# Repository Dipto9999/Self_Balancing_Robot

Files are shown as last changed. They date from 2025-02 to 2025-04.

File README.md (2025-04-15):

# WALL-E (Self Balancing Robot)

## Contents

* [Overview](#overview)
  * [Features](#features)
  * [Components](#components)
* [System Design](#system-design)
  * [Functional Diagram](#functional-diagram)
  * [Architecture Diagram](#architecture-diagram)
* [Robot Firmware](#robot-firmware)
  * [Arduino](#arduino)
  * [STM32](#stm32)
* [User Software](#user-software)
  * [Driver App](#driver-app)
  * [Dashboard App](#dashboard-app)
* [Demonstration](#demonstration)
* [Credit](#credit)

---

## Overview

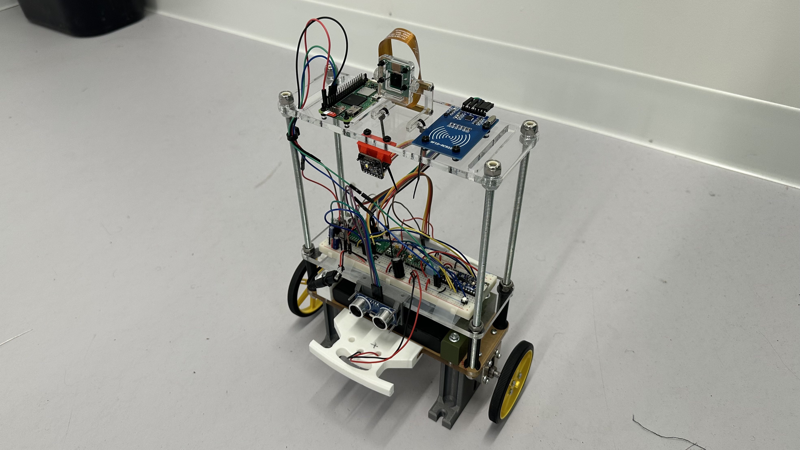
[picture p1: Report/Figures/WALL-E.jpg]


We designed **WALL-E**, an autonomously balancing two-wheel robot driven wirelessly via Bluetooth.

### Features

WALL-E prioritizes safe navigation and secure access.

- Detects the nearby environment (i.e. obstacles, color recognition)
- Prevents unauthorized control with **RFID** authentication and BLE pairing code.
- Generates live camera feed and uploads to **AWS S3** cloud storage.

### Components

- **Microcontrollers**:
  - Arduino Nano 33 BLE Sense Rev2 (Balancing & BLE)
  - STM32L051K8T6 (Environmental Sensors, Auth)
  - Raspberry Pi Zero 2 W (Camera Feed)

- **Sensors and Modules**:
  - BMM150 IMU
  - HC-SR04 Ultrasonic Distance Sensor
  - TCS34725 Color Sensor
  - RC522 RFID Module
  - CEM-1302 Buzzer
  - Freenove 5MP Camera

- **Actuation**:
  - DRV8833 Motor Drivers
  - Pololu 37D DC Motors

---

## System Design

### Functional Diagram

<p align="center">
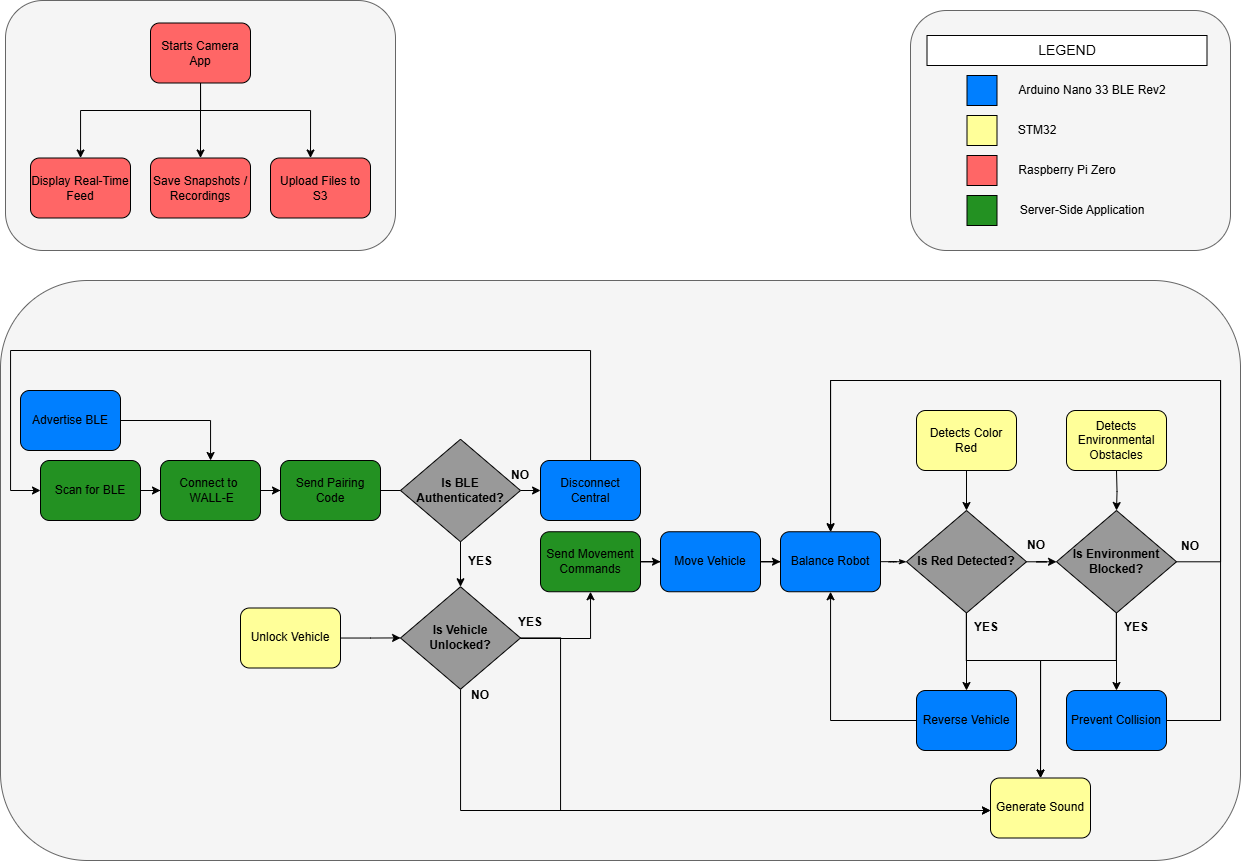
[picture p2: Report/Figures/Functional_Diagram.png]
Functional Diagram
  
</p>

### Architecture Diagram

<p align="center">
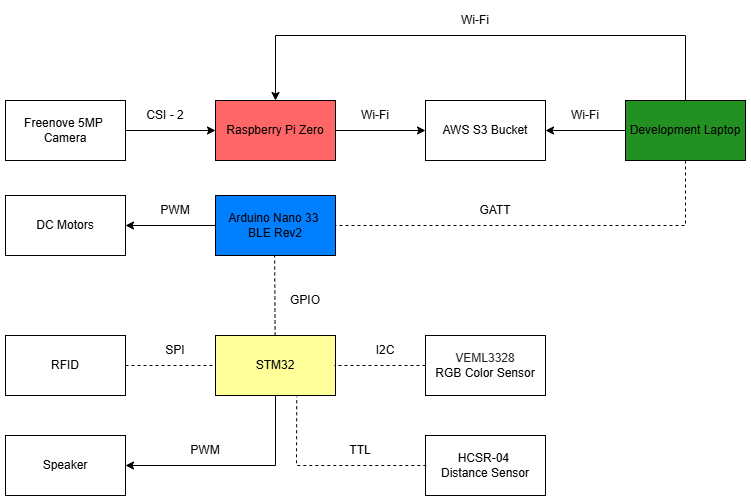
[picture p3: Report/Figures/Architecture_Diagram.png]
Architecture Diagram
  
</p>

---

## Robot Firmware

### Arduino

- Autonomously balances robot with closed-loop control system (i.e. PID controller).
- Uses complementary filter to measure angular input from accelerometer and gyroscope sensors.
- Drives motors by generating PWM (slow decay) output to DRV8833 chip.
- Uses statemachine to prioritize balancing / movement functionality.
    - Injects noise (i.e. angular offset, PWM signals) to induce movement along axis / turning.

<p align="center">
  <i>
    Source Code in <a href="/Arduino_Firmware/main">Arduino_Firmware</a> directory.
  </i>
</p>

### STM32

- Handles auxiliary features to reduce computational load on Arduino.
    - **Distance Sensing**: Toggles GPIO signal-low when object detected within 30cm.
    - **Color Detection**: Toggles GPIO signal-low when red is detected. WALL-E avoids red-lights at all costs.
    - **RFID Authentication**: Verifies UID and signals Arduino on success.
    - **Buzzer**: Alerts user on successful auth, errors, or warnings via PWM tone generation.

<p align="center">
  <i>
    Source Code in <a href="/STM32_Firmware">STM32_Firmware</a> directory.
  </i>
</p>

## User Software

### Robot Driver App

- **Flask** web application hosted via **ngrok** for mobile access
- Uses **GET**/**POST** requests to update server with **UI** updates and perform Bluetooth operations.
- Handles **BLE** pairing authentication in backend (i.e. without affecting user experience).

<p align="center">
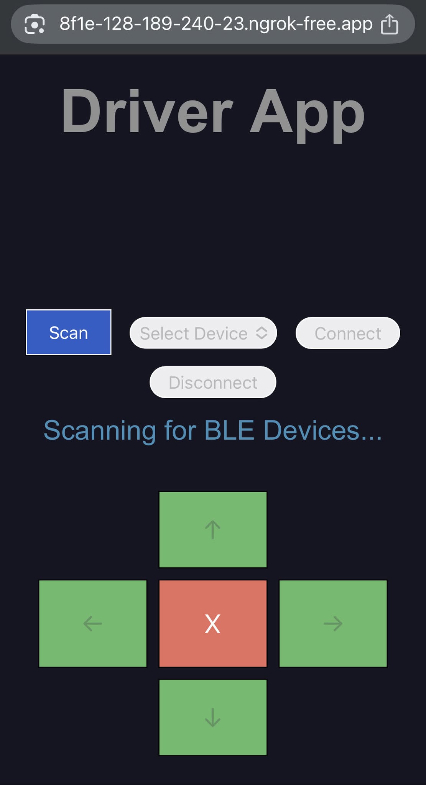
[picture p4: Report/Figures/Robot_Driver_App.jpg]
Robot Driver App on iPhone 14
    
</p>

<p align="center">
  <i>
    Source Code in <a href="/Driver_App">Driver_App</a> directory.
  </i>
</p>

### Dashboard App

- **Python** application with live camera stream on **Tkinter GUI**.
    - Camera runs at ~20 FPS with reduced resolution for performance on Pi Zero 2 W.
- Snapshot and recording functionality with automatic upload to **AWS S3** bucket.

<p align="center">
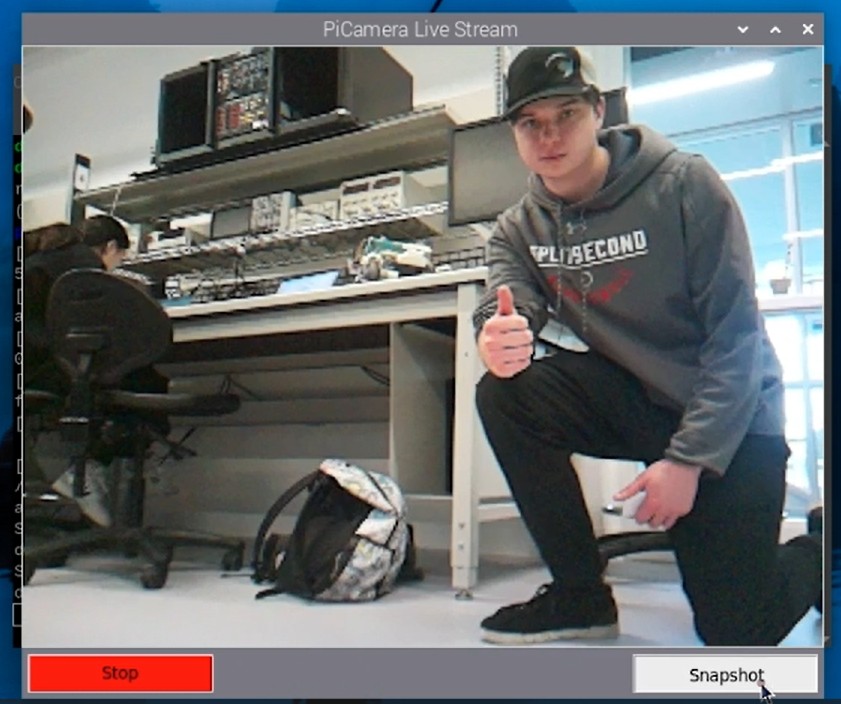
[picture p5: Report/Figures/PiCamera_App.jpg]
PiCamera Application
    
</p>

<p align="center">
  <i>
    Source Code in <a href="/Dashboard_App">Dashboard_App</a> directory.
  </i>
</p>

---

## Demonstration

Watch our final robot demonstration here:
📽️ [YouTube Demo](https://youtu.be/UMmxqQl_EAc?si=lTu5z8PBC82dAWoi)

## Report

Read our final project report here:
📝 [Project Report](/Report/ELEC391_B17_ProjectReport.pdf)

## Credit

This was completed as part of the **ELEC 391 - Design Studio** project course in **The University of British Columbia Electrical and Computer Engineering** undergraduate program.

**Team B-17**
- Muntakim Rahman
- Tomaz Zlindra
- Xianyao Li

Special thanks to **Dr. Joseph Yan** for tremendous support and guidance.

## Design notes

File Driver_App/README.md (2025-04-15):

# Robot Driver App

This **Flask** application is used to send movement commands to WALL-E. This is run and hosted on a local server. A secure public URL
is temporarily created with **ngrok**. Traffic is forwarded to the local server without the need for deployment.

## Host Application

<b>Run the following commands:</b>
<ul>
    <li>Run `python app.py`</li>
    <li>Run `ngrok http http://localhost:5000`</li>
</ul>

<p align="center">
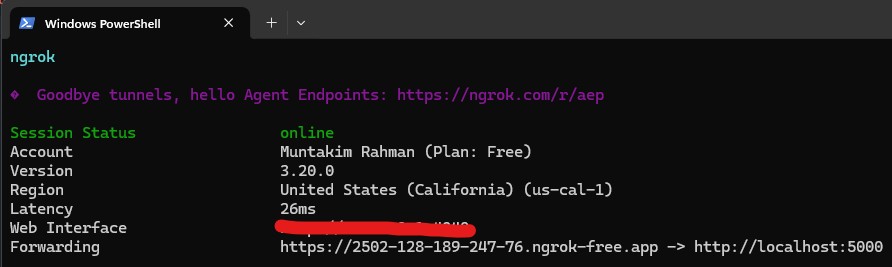
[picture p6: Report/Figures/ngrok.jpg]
ngrok Forwarding
  
</p>

<div style="text-align: center;"><i>The app can be accessed via the forwarding URL.</i></div>

# Desktop App

This **Tkinter** application is used to send movement commands to WALL-E and update PID parameters for balancing.

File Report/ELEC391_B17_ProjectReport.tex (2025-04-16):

\documentclass{article}
\usepackage[margin=0.8in]{geometry} % Set margins to 0.8 inch
\usepackage{graphicx} % Required for inserting images
\usepackage{hyperref}
\usepackage{tabularx}
\usepackage{amsmath}
\usepackage{amssymb}
\usepackage{float}
\usepackage{listings}
\usepackage{xcolor}
\usepackage[backend=biber,style=ieee,]{biblatex}

\lstset{
  basicstyle=\ttfamily\footnotesize,
  breaklines=true,
  breakatwhitespace=true,
  frame=single,
  numbers=left,
  numberstyle=\tiny,
  keywordstyle=\color{blue},
  commentstyle=\color{gray},
  stringstyle=\color{red},
  tabsize=4,
  captionpos=b,
  mathescape=true,
  literate={_}{\_}1  % <-- add this line
}

\addbibresource{ref.bib}

\setlength{\parindent}{0pt}

\title{
    \Huge \textbf{Self-Balancing Robot}

    \vspace{100pt}

    \large Course: ELEC 391 201 2024W2 \\[1em]
    \large Authors: Team B-17 (Tomaz Zlindra, Muntakim Rahman, Xianyao Li) \\[1em]
    \large Instructors: Dr.\ Joseph Yan and Dr.\ Cristian Grecu \\[1em]
    \large Submission Date: 2025--04--13 \\
}

\date{} % Remove default date

\begin{document}

\pagenumbering{gobble} % Suppress page numbering for the title page
\maketitle

\newpage % Start numbering after title page
\pagenumbering{arabic} % Restart numbering at 1

\tableofcontents % Generate Table of Contents

\newpage % Start main content

\section{Introduction}

\begin{minipage}{\linewidth}
    This project focused on the design and development of a self-balancing robot which can be driven via \textbf{Bluetooth Low Energy (BLE)}.
    The robot autonomously maintained its upright position with real-time feedback from an on-board microcontroller \textbf{IMU},
    with closed-loop controller continuously adjusting the motors to correct for angular tilt. \\
\end{minipage}

\begin{figure}[H]
    \centering
    {\setlength{\fboxsep}{0pt}\fbox{}}
    \caption{WALL-E: Self-Balancing Robot Prototype}
    \label{fig:wall_e}
\end{figure}

\begin{minipage}{\linewidth}
    It was also designed to support wireless control from a human user, responding to directional commands from a mobile device.
    The system integrates both stability and mobility, demonstrating precise control in dynamic environments.
\end{minipage}

\section{Requirements, Specifications and Constraints}

\subsection{Functional Requirements}

Table~\ref{tab:functional_requirements} lists the functional requirements of the self-balancing robot. These are prioritized by category as
either a core or additional feature. \\

\begin{table}[H]
    \centering
    \renewcommand{\arraystretch}{1.3} % Increase row height for readability
    \begin{tabularx}{\textwidth}{|c|X|c|}
        \hline
        \textbf{ID} & \textbf{Requirement Description} & \textbf{Priority} \\
        \hline
        FR1 & The robot must balance on a flat surface by controlling the DC motors. & Core \\
        \hline
        FR2 & The robot must maintain balance while driven externally on a flat surface. & Core \\
        \hline
        FR3 & The robot must maintain balance while turning at a reasonable speed. & Core \\
        \hline
        FR4 & The robot must move forward and backward under external control. & Core \\
        \hline
        FR5 & The robot must be controlled via Bluetooth with four directional commands. & Core \\
        \hline
        FR6 & The robot must be able to recover when disturbed & Core \\
        \hline
        FR7 & The robot is powered solely by a pack of 8 $\times$ 1.2V rechargeable batteries. & Core \\
        \hline
        FR8 & The distance sensor must detect obstacles and stop when it gets too close to an object & Additional Feature \\
        \hline
        FR9 & The color sensor must be able to detect at least one color & Additional Feature \\
        \hline
        FR10 & The RFID module must authenticate an RFID tag and prevent unauthorized operation. & Additional Feature \\
        \hline
        FR11 & The Raspberry Pi Zero must process and transmit a camera feed through Pi Connect & Additional Feature \\
        \hline
        FR12 & The AWS Bucket should store all the saved images and videos from the camera & Additional Feature \\
        \hline
    \end{tabularx}
    \caption{Functional Requirements of the Self-Balancing Robot}
    \label{tab:functional_requirements}
\end{table}

The core functionality of the robot relate to its ability to autonomously balance itself and be driven
by a human user via \textbf{BLE}. The additional features were designed to enhance the robot's capabilities, in detecting environmental factors and
providing useful information to the user.

\subsection{Performance Requirements}
Table \ref{tab:performance_requirements} outlines the performance requirements for the self-balancing robot, providing specific quantitative targets to assess the system's effectiveness.
These closely align with the functional requirements, but with the addition of measurable criteria—such as recovery angle, speed and transmission speed.

\begin{table}[H]
    \centering
    \renewcommand{\arraystretch}{1.3} % Increase row height for readability
    \begin{tabularx}{\textwidth}{|c|X|c|}
        \hline
        \textbf{ID} & \textbf{Requirement Description} & \textbf{Priority} \\
        \hline
        PR1 & The robot must respond to a $15 ^\circ$  disturbance and re-balance & Core \\
        \hline
        PR2 & The robot must maintain balance with a positional drift of less than $15$ cm over $10$s on a flat surface. & Core \\
        \hline
        PR3 & The Bluetooth latency for control commands must be less than $100$ ms. & Core \\
        \hline
        PR4 & The robot must be able to maintain a Bluetooth connection within a range of at least $5$m. & Core \\
        \hline
        PR5 & The robot must be to move forward, backward, left ($45^\circ$) and right ($45^\circ$) within 5 seconds & Core \\
        \hline
        PR6 & The obstacle detection system must stop the robot within $1$cm of an obstacle detected between $2-30$cm. & Additional Feature \\
        \hline
        PR7 & The color sensor must identify red and respond accordingly within $100$ms & Additional Feature \\
        \hline
        PR8 & The RFID reader must successfully detect and authenticate tags within $1$s. & Additional Feature \\
        \hline
        PR9 & The Raspberry Pi Zero must transmit a camera feed at no less than $1$ FPS. & Additional Feature \\
        \hline
    \end{tabularx}
    \caption{Performance Requirements of the Self-Balancing Robot}
    \label{tab:performance_requirements}
\end{table}

By translating functional goals into performance metrics, we ensured that the robot's behavior could be consistently validated against clearly defined benchmarks.
This approach helped guide both the design process and iterative improvements throughout development.

\subsection{Constraints}

\subsubsection{Financial}
This project operated under a strict financial constraint, with a maximum budget of \$65 allocated specifically for additional
features (excluding taxes and shipping). To maximize the number of features within this limit, we opted to purchase components from alternative vendors when they offered more competitive prices than DigiKey. We determined that the most effective use of our budget was to prioritize implementing multiple smaller features,
rather than allocating the entire amount toward a single major feature. \\

\textit{For a detailed breakdown of the expenses and financial details, refer to the following \href{https://docs.google.com/spreadsheets/d/1k2FMDTlyxH50N65zvA1Ss5obWOlDuc3JaWVVDWrQ88E/edit?usp=sharing}{Google Sheet}.
The high-level breakdown is also included in the Appendix (i.e. Figure~\ref{fig:financials}).}

\subsubsection{Temporal}

Although the final project deliverable was due on \textbf{2025--04--08}, we set several soft deadlines along the way to track our progress
and prevent last-minute workload buildup. Some of the main deadlines are shown below.

\begin{minipage}{\linewidth}
    \begin{description}
        \item[2025--02--28:] Motor Control PWM for Arduino
        \item[2025--03--06:] Completed BLE Integration with Python App
        \item[2025--03--07:] Completed Distance Sensor and Color Sensor STM32 Firmware
        \item[2025--03--13:] Completed PID k-value Calculations
        \item[2025--03--14:] Completed RFID STM32 Firmware
        \item[2025--03--20:] Completed Raspberry Pi App
        \item[2025--03--21:] Completed Speaker Integration STM32 Firmware
        \item[2025--03--28:] Completed Robot Balancing
    \end{description}
\end{minipage}

Although most deadlines were met, a few, particularly the robot balancing milestone were not achieved on time. This delay was primarily due to some questionable firmware design decisions that introduced unforeseen challenges. Fortunately, these issues were resolved, and the system was successfully completed in the end.

\subsubsection{Materials}
For the custom construction of our self-balancing robot, we were limited to using thick plastic for laser cutting and standard 3D printing filament, as these materials were readily available and did not impact our budget. While other materials—such as aluminum, carbon fiber, or specialized fasteners—could have offered enhanced strength or reduced weight, they would have required additional spending from our \$65 budget. To stay within our constraints, we opted not to purchase any external materials and instead focused on optimizing our design using the provided components and available fabrication methods.

\subsubsection{Environmental}
The performance of a self-balancing robot can be significantly affected by environmental constraints such as battery levels, electromagnetic interference (EMI), temperature, and terrain conditions. Low battery voltage can reduce motor torque and sensor accuracy, leading to instability. EMI from nearby motors or power electronics can disrupt IMU readings and communication systems, making balance control less reliable. Temperature extremes can alter sensor calibration and battery efficiency, while uneven or slippery terrain can interfere with traction and cause the robot to lose balance. These factors must be carefully considered to ensure reliable operation in real-world environments.

\section{Conceptual Design}

\subsection{High-level Functional Diagram}

\begin{figure}[H]
    \centering
    
    \caption{High-level Functional Diagram}
    \label{fig:functional_diagram}
\end{figure}

\begin{minipage}{\linewidth}
    The functional diagram in Figure~(\ref{fig:functional_diagram}) highlights our system-design for enforcing secure access of the robot with
    \textbf{RFID} and \textbf{Bluetooth Low Energy (BLE)}. We prevent users from balancing or moving the robot without the required authentication. Once successful,
    the firmware was programmed to prioritize safe operation of the robot, while accounting for environmental factors such as distance and color detection. \\
\end{minipage}

\subsection{Architecture Diagram}

\begin{figure}[H]
    \centering
    
    \caption{Architecture Diagram}
    \label{fig:architecture_diagram}
\end{figure}

\begin{minipage}{\linewidth}
    The architecture diagram in Figure~(\ref{fig:architecture_diagram}) describes the interfaces between robot peripherals and the three boards
    used in the project: \\
\end{minipage}

\begin{itemize}
    \item \textbf{Arduino Nano 33 BLE Sense Rev2} was responsible for driving the motors and maintaining balance.
    \item \textbf{STM32L051K8T6} was responsible for environmental detection and physical authentication.
    \item \textbf{Raspberry Pi Zero W} was responsible for displaying and processing camera input for the user.
\end{itemize}

\textit{Note that we wirelessly accessed the \textbf{Raspberry Pi} and \textbf{Arduino} from a development machine.}

\section{Subsystem Design}

\subsection{Structural Design}

\subsubsection{Design Decisions}
Since the transfer function of the robot was derived under the assumption that
the center of mass of the pendulum is perfectly centered, the structural design
follows the principle of evenly distributing mass to ensure that the center of
mass is as close as possible to the rotor axis.

\

Another design decision we made was to mount the third layer as high as
possible. This choice addresses the fact that the plant is a nonlinear and
inherently unstable system, which can only be effectively controlled within a
region where it can be approximated as linear. To evaluate the impact of the
third layer's height on system behavior, we simulated the plant's step response
at different mounting heights:

\begin{figure}[H]
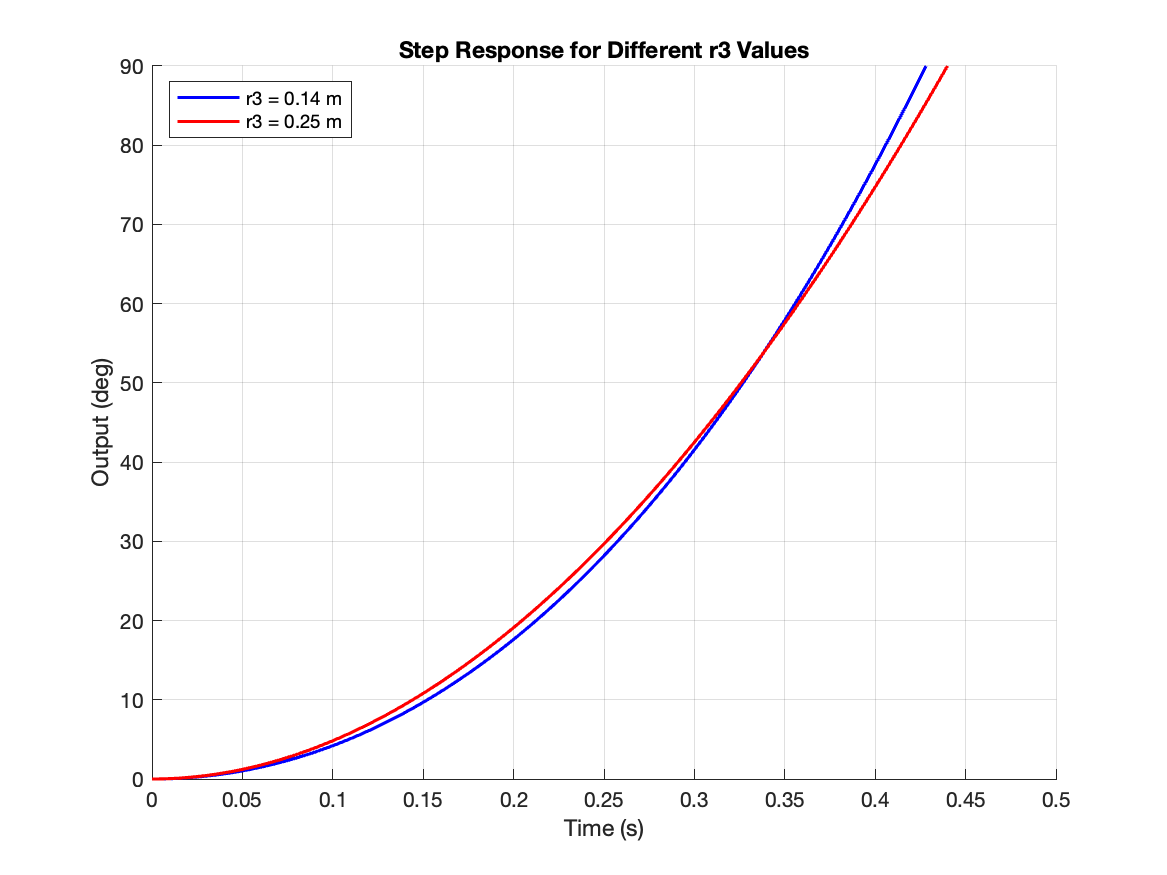
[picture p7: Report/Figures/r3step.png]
    \centerline{\fbox{}}
    \caption{Step Response of the Plant with Different Height of the Third Layer}
\end{figure}

As shown in the figure, increasing the height of the third layer results in a
step response that more closely resembles that of a linear system, making it
easier to control.

\begin{figure}[H]
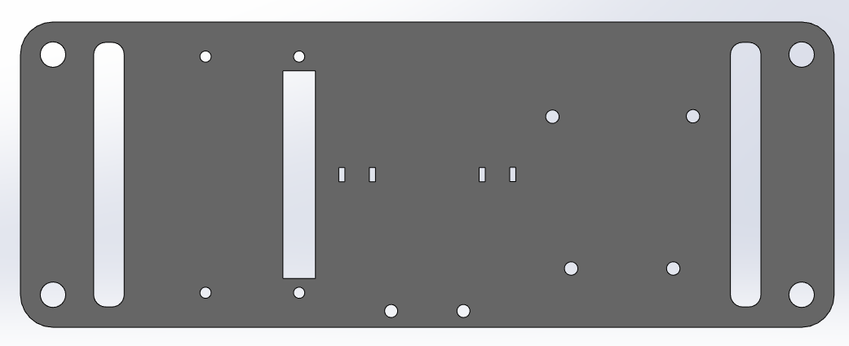
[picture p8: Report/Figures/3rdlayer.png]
    \centerline{}
    \caption{Design of the Third Layer}
\end{figure}

\subsubsection{Third Layer Design}
On the third layer, we need to mount the Raspberry Pi, color sensor, RFID
reader, and camera. The four mounting holes on the left side are for securing
the Raspberry Pi, while the four holes on the right are for the RFID reader.
These holes are positioned to ensure that both components are centered relative
to the third layer once mounted.

At the bottom, two mounting holes are used to attach the L-stand for the color
sensor. Since we only have one color sensor, its placement causes a deviation in
the center of mass. To compensate for this imbalance, the camera is zip-tied at
the center, allowing its position to be adjusted to help realign the center of
mass. Although not shown in the figure, two distance sensors are also mounted on
the second layer symmetrically.

\subsubsection{L-stand Design}
The design of the L-stand is shown below:
\begin{figure}[H]
    \centering
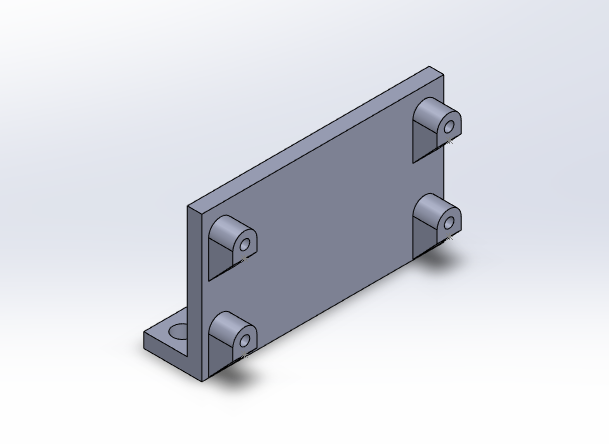
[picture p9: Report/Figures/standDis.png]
    {\setlength{\fboxsep}{0pt}\fbox{}}
    \caption{Design of the L-stand for Mounting the Distance Sensor}
\end{figure}

The L-stand includes four columns to provide clearance for the distance sensor,
as there are components located on the back of the PCB. Ribs are added beneath
each column to address potential issues during 3D printing. Since overhangs can
lead to poor print quality or failed prints, the ribs provide structural support
under the columns, eliminating overhangs and making the printing process more
reliable and efficient.

\

The L-stand for the color sensor follows the same design principles with
different dimension, thus is not shown here.

\subsection{PID Modeling and Simulation}
\subsubsection{Robot Parameters}

With the corrected transfer function, we need to find the values of the
parameters in order to get the transfer function. \\

We start with the motor constants. For $K_t$, from the datasheet we know
that the stall current is 5.5 A and the torque at 12 V is 85 kg$\cdot$mm, or
0.83N$\cdot$m, we can then get the value of $K_t$ by dividing the torque by the
stall current, which is 0.1516. \\

For $K_e$, from the datasheet we know that the free run speed of the rotor
without the gearbox is 1047.19 rad/s, we can then get the value of $K_e$ by
dividing the load voltage 12 V by the free run speed of the rotor, which is
0.01146. \\

To obtain the moment of inertia of the pendulum $J_p$, we need to simplify the
plant model. The robot consists of four rods and three layers. Assuming the
center of mass is perfectly centered, the four rods can be approximated as a
single equivalent rod located at the center of the three layers. Similarly, the
three layers can be modeled as three point masses, which are further simplified
into a single point mass located at their collective center of mass. The
resulting simplified model consists of a single rod rotating about one end and a
point mass positioned at the center of mass of the three layers. \\
\begin{figure}[H]
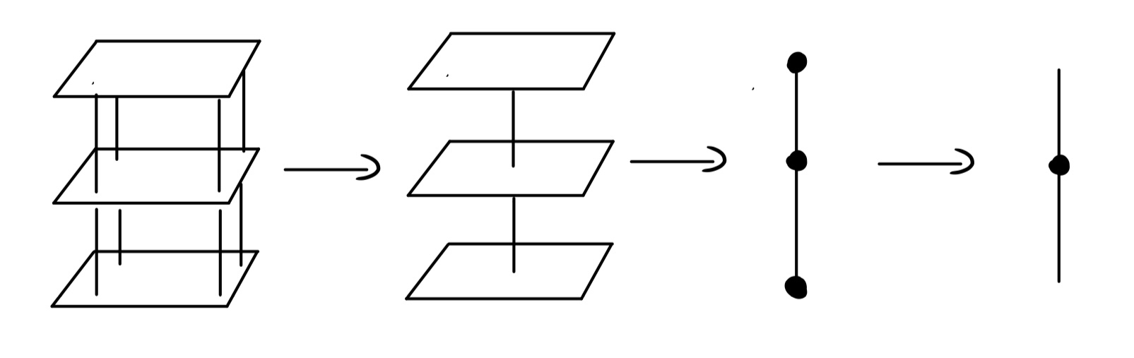
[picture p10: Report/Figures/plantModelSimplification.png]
    \centerline{}
    \caption{Simplification of the Plant Model}
\end{figure}

All of the other parameters can either be measured directly, or are negligible
and have minimal impact on the overall transfer function. \\

\subsubsection{Transfer Function}

Considering the difficulty of deriving the transfer function from first
principles, and given the abundance of studies on the same topic, we chose to
reference a published paper for guidance \cite{suspaper}. However, upon
reviewing the paper, we identified errors in part of the derivation: \\

Assuming the correctness of
\begin{align}
K_t \frac{V_s - K_e \dot{\theta}_m}{R_a} &= J_m \ddot{\theta}_m + \tau_w + b \dot{\theta}_m \\
\tau_w &= J_w \ddot{\theta}_w - F_{pH} r_w + m_w \ddot{\theta}_w r_w^2 \\
F_{pH} &= m_p (r_w \ddot{\theta}_w + l_g \ddot{\theta}_p) \\
F_{pH} l_g &= J_p \ddot{\theta}_p \\
\theta_m &= \frac{\theta_w}{G_r}
\end{align}
Substitute (3) into (4) gives:
\begin{align*}
m_p (r_w \ddot{\theta}_w + l_g \ddot{\theta}_p) l_g &= J_p \ddot{\theta}_p \\
m_p l_g r_w \ddot{\theta}_w + m_p l_g^2 \ddot{\theta}_p &= J_p \ddot{\theta}_p \\
m_p l_g r_w \ddot{\theta}_w &= (J_p - m_p l_g^2) \ddot{\theta}_p \\
\ddot{\theta}_w &= \frac{J_p - m_p l_g^2}{m_p l_g r_w} \ddot{\theta}_p \\
\theta_w &= \frac{J_p - m_p l_g^2}{m_p l_g r_w} \theta_p
\end{align*}
So Eq. 4 in the paper is incorrect. The \(\tau_w\) in denominator should be \(r_w\). The signs are also wrong.
Substitute (3) into (2) gives:
\begin{align*}
\tau_w &= J_w \ddot{\theta}_w - m_p (r_w \ddot{\theta}_w + l_g \ddot{\theta}_p) r_w + m_w \ddot{\theta}_w r_w^2 \\
&= (J_w + (m_w - m_p) r_w^2) \ddot{\theta}_w - m_p l_g r_w \ddot{\theta}_p
\end{align*}
Substitute the above and (5) into (1) and expand the first fraction:
\[
\frac{K_t}{R_a} V_s - \frac{K_t}{R_a} \frac{K_e}{G_r} \dot{\theta}_w - \frac{b}{G_r} \dot{\theta}_w - (J_w + (m_w - m_p) r_w^2) \ddot{\theta}_w + m_p l_g r_w \ddot{\theta}_p = \frac{J_m}{G_r} \ddot{\theta}_w
\]
Move the angle terms to RHS and flip both sides:
\begin{align*}
\left( \frac{K_t}{R_a} \frac{K_e}{G_r} + \frac{b}{G_r} \right) \dot{\theta}_w + \left[ \frac{J_m}{G_r} + J_w + (m_w - m_p) r_w^2 \right] \ddot{\theta}_w - m_p l_g r_w \ddot{\theta}_p &= \frac{K_t}{R_a} V_s
\end{align*}
Substitute the expression of \(\theta_w\) in terms of \(\theta_p\):
\begin{align*}
(J_p - m_p l_g^2) \left( \frac{K_t}{R_a} \frac{K_e}{G_r} + \frac{b}{G_r} \right) \dot{\theta}_p + \left[ (J_p - m_p l_g^2) \left[ \frac{J_m}{G_r} + J_w + (m_w - m_p) r_w^2 \right] + (m_p l_g r_w)^2 \right] \ddot{\theta}_p \\= \frac{K_t}{R_a} (m_p l_g r_w) V_s
\end{align*}
Laplace transform:
\begin{multline*}
\theta_p(s) \left[ (J_p - m_p l_g^2) \left( \frac{K_t}{R_a} \frac{K_e}{G_r} + \frac{b}{G_r} \right) s + \left[ (J_p - m_p l_g^2) \left[ \frac{J_m}{G_r} + J_w + (m_w - m_p) r_w^2 \right] + (m_p l_g r_w)^2 \right] s^2 \right]
\\= \frac{K_t}{R_a} (m_p l_g r_w) V_s(s)
\end{multline*}
Hence the final transfer function:
\[
\frac{\theta_p}{V_s}(s) = \frac{\frac{K_t}{R_a} (m_p l_g r_w)}{\left[ (J_p - m_p l_g^2) \left[ \frac{J_m}{G_r} + J_w + (m_w - m_p) r_w^2 \right] + (m_p l_g r_w)^2 \right] s^2 + (J_p - m_p l_g^2) \left( \frac{K_t}{R_a} \frac{K_e}{G_r} + \frac{b}{G_r} \right) s}
\]
The definition of the parameters can be found in the paper. \\

Plug in the parameters we acquired, the resulting open loop transfer function is:
\[
\frac{\theta_p}{V_s}(s) = \frac{977.5}{s^2+0.3439s}
\]
Notice that the moment of inertia of the wheel and the rotor ($J_m \& J_r$) and
friction $b$ are approximated to zero, This is because their magnitudes are
negligible compared to other parameters in the system, thus they have
minimal impact on the overall transfer function.

\subsubsection{PID Parameter Calculation}

From the previously derived transfer function, we observe that the two open-loop
poles are located at $0$ and $-0.3439$, indicating that the system is unstable. To
stabilize the system, a feedback control loop must be introduced to shift the
poles of the closed-loop transfer function to stable locations. To determine the
PID parameters, we can apply the pole placement method: \\

Assuming that we want the resulting poles to be placed at $P_A$ and $P_B$, the
denominator of the resulting transfer function is:
\[
(s-P_A)(s-P_B)
\]
This can be written explicitly as:
\[
s^2 - (P_A + P_B)s + P_AP_B
\]
With a PD controller, the characteristic equation is:
\[
s^2 + (K \cdot K_d - (P_1 + P_2))s + P_1P_2 + KK_p
\]
Where $P_1$ and $P_2$ are poles of the open loop transfer function, $K$ is the
DC gain of the transfer function, which is 977.5.

\

We can relate the above two equations and the following equations can be obtained:
\begin{align*}
    P_AP_B &=  P_1P_2 + KK_p\\
    -(P_A + P_B) &= KK_d - (P_1 + P_2)
\end{align*}
The resulting PD gains will make the close loop transfer function be critically
damped and stable.

\

To determine the desired pole locations, we first need to select an appropriate
time constant $N$. By measuring the runtime of the main control loop, we found
the worst-case execution frequency to be 25 Hz. According to the Nyquist
theorem, the sampling rate must be at least twice the highest frequency
component to accurately capture the system dynamics. Therefore, the maximum
allowable control bandwidth is $12.5$ Hz, corresponding to a minimum time constant
of approximately $0.08$. To ensure stability and responsiveness while staying
within this limit, we chose a time constant of $0.25$ s, which places the
desired pole at $-8\pi$ and the resulting $K_p$ and $K_d$ are $0.6462$ and $0.0511$,
respectively.

\

The I term is added after to address the drifting issue we encountered during
the testing. The value of $K_i$ was found by trial and error, and the final
value of $K_i$ is $11.5$.

\subsubsection{Simulink Simulation}

Simulink is used to validate the design of the PID controller. The model is
shown below:
\begin{figure}[H]
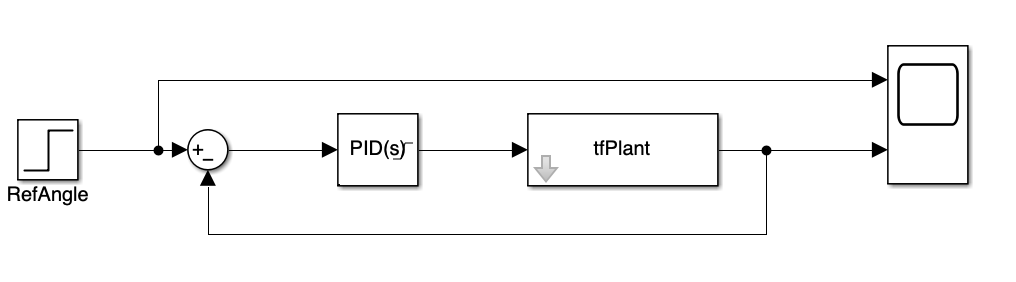
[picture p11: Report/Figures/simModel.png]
    \centerline{}
    \caption{Simulink Model for the Bot}
\end{figure}
The step responses of the system under filter coefficient N = 50 and N = 25 were
simulated to evaluate the performance of the robot under best- and worst-case
scenarios:
\begin{figure}[H]
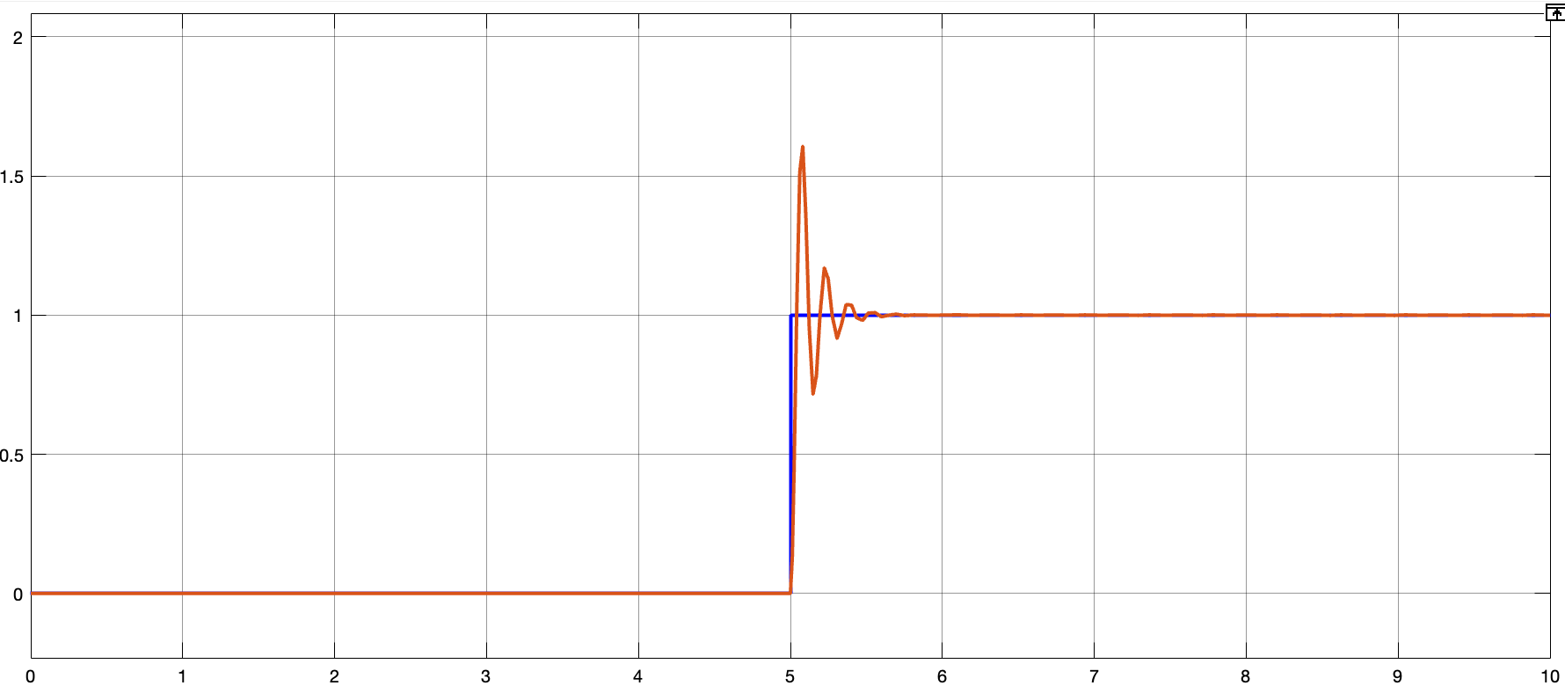
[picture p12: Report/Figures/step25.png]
    \centerline{}
    \caption{Step Response of the System with N = 25}
\end{figure}
\begin{figure}[H]
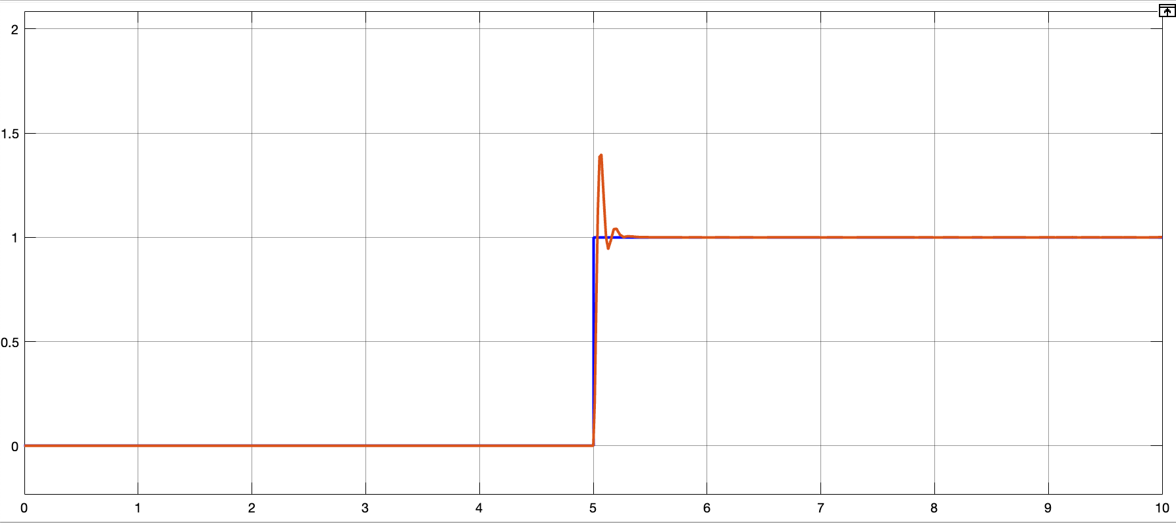
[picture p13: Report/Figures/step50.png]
    \centerline{}
    \caption{Step Response of the System with N = 50}
\end{figure}
We can see that for both cases the system is stable, with different degree of
overshoot. This implies that the design of the PID controller is effective.

\subsection{Arduino Nano 33 BLE Sense Rev2}

\begin{figure}[H]
    \centering
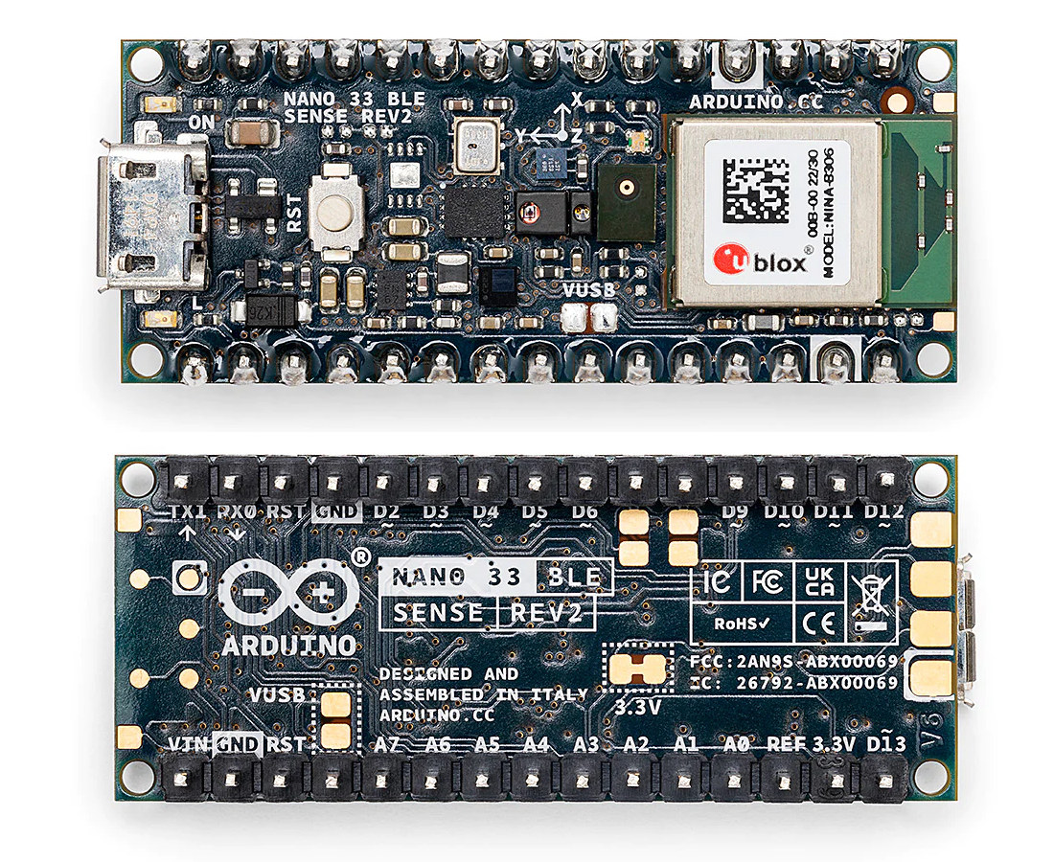
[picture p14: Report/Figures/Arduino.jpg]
     % Adjust width as needed
    \caption{Arduino Nano 33 BLE Sense Rev2}
    \label{fig:arduino}
\end{figure}

\begin{minipage}{\linewidth}
    The \textbf{Arduino Nano 33 BLE Sense Rev2}  is a compact and powerful microcontroller board
    designed for low-power applications. It features the Nordic \textbf{nRF52840} chipset,
    which supports \textbf{BLE} communication, includes a range of built-in sensors,
    including a 9-axis IMU (accelerometer, gyroscope, and magnetometer).
    These integrated features make it well-suited for IoT, sensor-based applications, and portable devices. \\

    This made it the ideal choice for our self-balancing robot project and was responsible for many of the core features.
    It integrated key core components in this project, particularly the \textbf{IMU} and the \textbf{BLE} module. \\
\end{minipage}

\subsubsection{Arduino IDE}

\begin{minipage}{\linewidth}
    The \textbf{Arduino IDE} was integral in quickly testing new firmware changes to the board with built-in compilation and flashing tools.
    The extensive library support significantly streamlined the development process, reducing the need for bare metal programming and allowing us to focus on the functionality.
\end{minipage}

\subsubsection{IMU Angle Measurement}
\label{sec:angle}

\begin{figure}[H]
    \centering
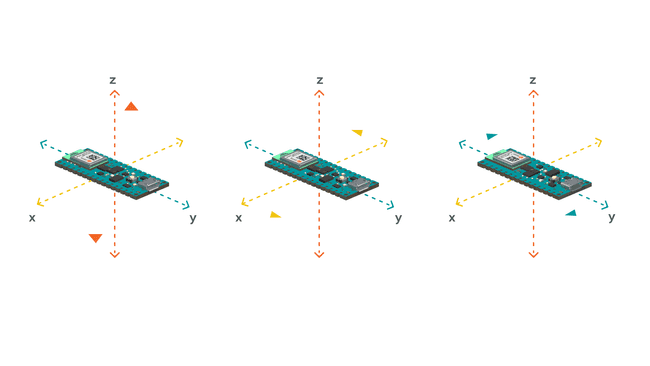
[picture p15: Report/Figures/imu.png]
     % Adjust width as needed
    \caption{IMU}
    \label{fig:imu}
\end{figure}

\begin{minipage}{\linewidth}
    The \textbf{Inertial Measurement Unit (IMU)} was a critical microcontroller component for measuring velocity, orientation, and
    gravitational forces. This enabled the tracking of motion and orientation of the \textbf{Arduino} in three-dimensional space. \\

    We used the accelerometer to measure linear acceleration and the gyroscope to monitor rotational
    movement. Both of these sensors had advantages and disadvantages, as shown in Table~\ref{tab:imu_sensors}.
    By combining them, we ensured reliable and accurate angle measurements for optimized balancing in the control feedback loop.
\end{minipage}

\subsubsection{Complementary Filter}

% \begin{figure}[H]
%     \centering
%     \includegraphics[width=0.6\textwidth]{Figures/complementary_filter.png} % Adjust width as needed
%     \caption{Complementary Filter Feedback Diagram}
%     \label{fig:complementary_filter}
% \end{figure}

\begin{minipage}{\linewidth}
    The solution to combine the strengths of both sensors was to use a complementary filter,
    which combines the accelerometer and gyroscope readings with their respective normalized weights. \\

    Since the gyroscope provided a rough estimate of the angle change, this was essential for detecting quick movements. \\
\end{minipage}

The formula used for the complementary angle is:

\[
\theta_n = k(\theta_{n-1} + \theta_{g,n}) + (1-k)\theta_{a,n},
\]

where:
\begin{itemize}
    \item $\theta_n$ is the current complementary angle,
    \item $\theta_{n-1}$ is the previous complementary angle,
    \item $\theta_{g,n}$ is the current gyroscope angle,
    \item $\theta_{a,n}$ is the current accelerometer angle,
    \item $k$ is the normalized weight.
\end{itemize}

\begin{center}
    $\therefore$ From extensive testing, a value of $k = 0.95$ was selected. \\
\end{center}
\textit{Lower values of $k$
    caused the noise from the accelerometer to become significant, leading to large oscillations and loss of balance.
    Similarly, increasing $k$ was avoided. The gyroscope bias would accumulate quickly (i.e., without a reference point)
    and cause the robot to lose balance.
} \\

The code snippet for this exact implementation is demonstrated in Listing \ref{lst:arduino_angle_code}.

\subsection{Balancing}

\begin{minipage}{\linewidth}
    The most challenging part of this project was to implement the \textbf{PID} controller to balance the robot. Since we had closed-loop control,
    with the measured angle acting as feedback, it was crticial that we were able to act upon new measurements when determining the control signal. \\

    Initially, we attempted to implement these \textbf{Interrupt Service Routine (ISR)} to meet a designed control frequency of $20$ Hz.
    However, this proved to accumulate complications in firmware logic and was not able to provide the expected results. \\

    We ultimately designed a control loop, run in the main program. This followed the sequence shown in Figure~\ref{fig:control_loop_diagram}.
\end{minipage}

\begin{figure}[H]
    \centering
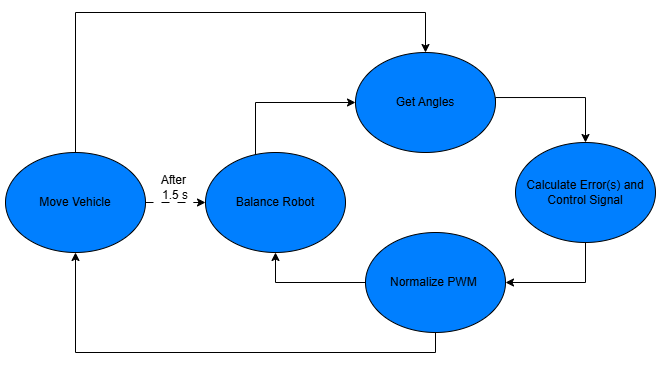
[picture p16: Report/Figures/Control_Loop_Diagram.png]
    
    \caption{Control Loop Diagram}
    \label{fig:control_loop_diagram}
\end{figure}

\begin{minipage}{\linewidth}
    This ensured that we were able to inject \textbf{PWM} signals to both motors, without the constraints typical of an \textbf{ISR}. At the same time,
    this ensured that the robot was acting upon the most recent measurements. \\

    The sign of the control signal determined whether to move the robot forward / backward to maintain balance. \\

    The source code for this implementation is shown in Listing \ref{lst:arduino_pid_code}, in the Appendix.
\end{minipage}

\subsubsection{Motor Control}

\begin{minipage}{\linewidth}
    To operate the robot wheels, we used the \textbf{DRV8833} motor driver to operate the robot with slow decay \textbf{PWM}.
    This entailed one of the motor terminals being driven to logic high, while the other was supplied the PWM signal. \\
\end{minipage}

\begin{figure}[H]
    \centering
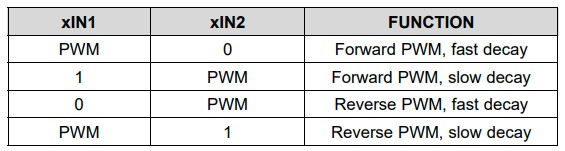
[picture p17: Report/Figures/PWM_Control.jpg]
    
    \caption{DRV8833 PWM Control}
    \label{fig:drv8833}
\end{figure}

\begin{minipage}{\linewidth}
    Supplying slow decay \textbf{PWM} enables the robot to gradually diminish its response to error angles, rather than abruptly stopping the motors.
    This was integral in ensuring the overall system behavior was stable and able to keep the robot balancing.

    \

    The source code for this implementation is shown in Listing \ref{lst:arduino_pwm_code}, in the Appendix.
\end{minipage}

\subsection{Movement}
\label{sec:movement}

\begin{minipage}{\linewidth}
    The robot was designed to move in four directions: \textbf{FORWARD, BACKWARD, LEFT, RIGHT}.
    As shown in Figure~\ref{fig:control_loop_diagram}, this was designed to be integrated into the control loop.  \\

    Balancing was the highest priority of the system at (almost) any given moment. To move the robot, we injected noise into the system for a short duration
    (i.e. $1.5$ s). After this, we returned to idle balancing to prevent the system from reaching a point of instability.

    \

    For the complete code snippet of this implementation, it can be found in Listing \ref{lst:arduino_movement_code}, in the Appendix.
\end{minipage}

\subsubsection{Forward/Backward Movement}

\begin{minipage}{\linewidth}
    The logic for moving the robot forward and backward was very simple. It was a matter of adjusting the setpoint angle on either side of the "zero point".
    This induced movement in the indended direction (without sacrificing balance). \\
\end{minipage}

\subsubsection{Left/Right Movement}

\begin{minipage}{\linewidth}
    The logic for moving the robot left and right was slightly more complicated and involved
    software logic to interchangeable turn and balance the robot. This can be summarized as follows: \\
\end{minipage}

\begin{itemize}
    \item \texttt{After (every) 3 iterations} of control loop : \texttt{balance robot}
    \item \texttt{If error angle $>$ allowable threshold} (i.e. $0.8^\circ$): \texttt{balance robot}
    \item Otherwise:
    \begin{itemize}
        \item To turn left: move left motor $CW$ and right motor $CCW$, with \textbf{PWM} adjusted by scale factor $0.6$
        \item To turn right: move left motor $CCW$ and right motor $CW$,  with \textbf{PWM} adjusted by scale factor $0.5$
    \end{itemize}
\end{itemize}

\subsection{Bluetooth Control}

\begin{minipage}{\linewidth}
    The robot was controlled via the \textbf{Arduino's} \textbf{Bluetooth Low Energy (BLE)} capabilities.
    The firmware was developed such that new connections need to be authorized by successfully transmitting
    the correct pairing code. This follows the workflow shown in Figure~\ref{fig:functional_diagram}. \\

    In order to send movement commands, the connection and authentication process must be successfully complete to ensure secure access. A key
    part of this process was to provide the expected pairing code to the microcontroller. \\
\end{minipage}

\begin{figure}[H]
    \centering
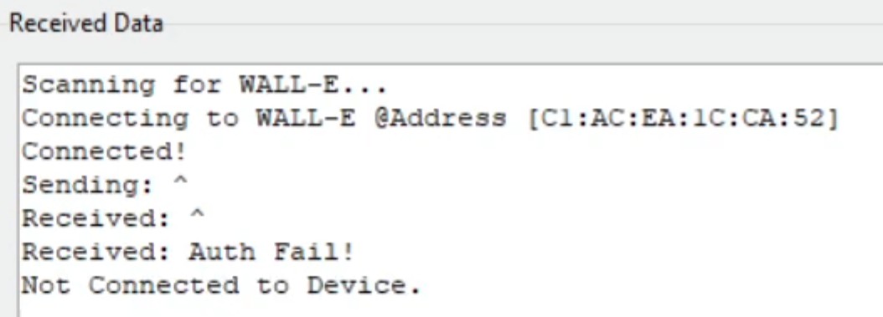
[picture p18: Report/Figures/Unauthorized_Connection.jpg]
    \fbox{}
    \caption{Unauthorized Bluetooth Connection}
    \label{fig:bluetooth_unauthorized}
\end{figure}

\begin{minipage}{\linewidth}
    If unsuccesful, the robot would immediately disconnect and await an authorized user as shown in Figure~\ref{fig:bluetooth_unauthorized}. \\

    The firmware is also designed such that movement commands are placed on a lower priority. Since \textbf{BLE} can be computationally expensive,
    we polled for new commands every $100$ ms in the main loop. This was done to ensure that the control functionality is placed at highest priority,
    and we can account for the infrequent nature of user driven commands.
\end{minipage}

\subsubsection{Robot Driver App}

\begin{minipage}{\linewidth}
    We developed a \textbf{Flask} application, which used \texttt{GET/POST} request \textbf{HTTP} methods
    to asynchronously request device information from the \textbf{HTML DOM} elements and send commands to the
    \textbf{Arduino} microcontroller. \\

    This application was run from our computer and temporarily hosted to the Internet using the \textbf{ngrok} tool.
    This enabled us to access the robot via public URL from other devices (including smartphones).
\end{minipage}\vspace{0.5cm}

\begin{figure}[H]
    \centering
    
    \caption{Robot Driver App on iPhone 14}
    \label{fig:ble_app}
\end{figure}

\begin{minipage}{\linewidth}
    The \textbf{Flask} application had the expected pairing code programmed in the source code such that users can easily connect to and control the robot.
    We programmed the \texttt{DRIVE, LEFT, RIGHT, BACK} commands to correspond to specific bytes to be transmitted via \textbf{BLE}. \\
\end{minipage}

\begin{center}
    This is shown in the code snippet in Listing \ref{lst:driver_app_code} in the Appendix.
\end{center}

\subsection{STM32L051K8T6 Microcontroller}
\label{sec:stm32}

\begin{figure}[H]
    \centering
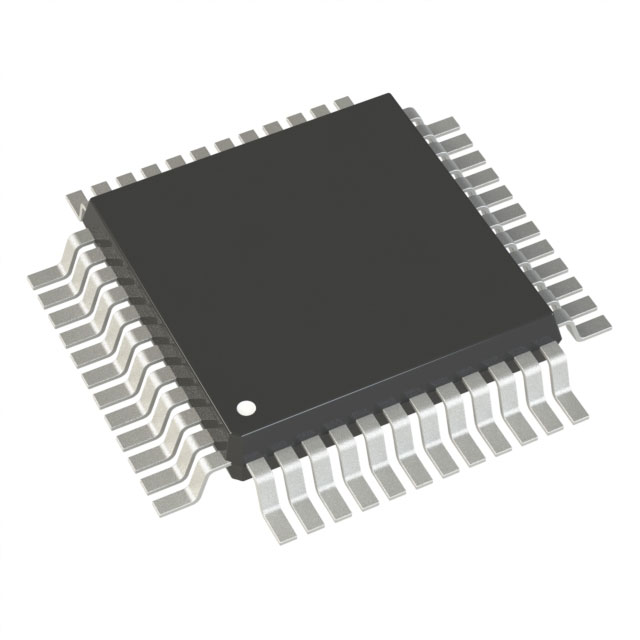
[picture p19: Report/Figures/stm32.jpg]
     % Adjust width as needed
    \caption{STM32L051K8T6 Microcontroller}
    \label{fig:stm32}
\end{figure}

The STM32L051K8T6 is a low-power microcontroller from STMicroelectronics, part of the STM32L0 series. It features an ARM Cortex-M0+ core running at up to 32 MHz, with 64 KB of flash memory and 8 KB of SRAM. For our project, this microcontroller was used to interface with the HC-SR04 (section \ref{sec:distancesensor}), TCS34725 (section \ref{sec:colorsensor}), RC522 (section \ref{sec:rfidsensor}) and the CEM-1202 (section \ref{sec:speaker}) modules. The pinout diagram is shown in Figure~\ref{fig:stm32_pinout_zoomed_in} (note that USART it was never used in the implementation).

\begin{figure}[H]
    \centering
    \begin{minipage}[b]{0.45\textwidth} % Adjust width as needed
        \centering
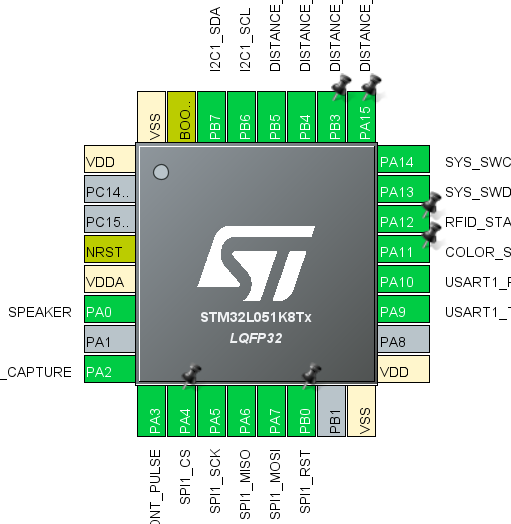
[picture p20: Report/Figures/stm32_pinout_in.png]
        
        \caption{Zoomed In Pinout}
        \label{fig:stm32_pinout_zoomed_in}
    \end{minipage} \hfill
    \begin{minipage}[b]{0.48\textwidth} % Adjust width as needed
        \centering
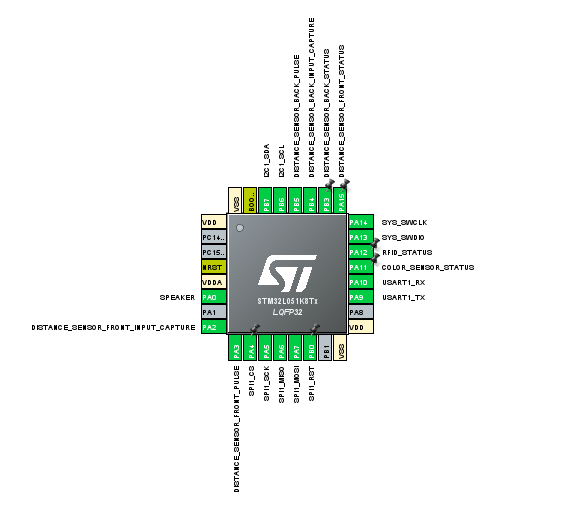
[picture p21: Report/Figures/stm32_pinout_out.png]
        
        \caption{Zoomed Out Pinout}
        \label{fig:stm32_pinout_zoomed_out}
    \end{minipage}
\end{figure}

To streamline the firmware development process for the STM32, we utilized the STM32Cube IDE, provided by STMicroelectronics. This development environment facilitated faster progress by offering built-in tools and libraries, allowing us to focus on application logic rather than dealing with bare-metal programming.

\subsubsection{Distance Sensing}
\label{sec:distancesensor}

\begin{figure}[H]
    \centering
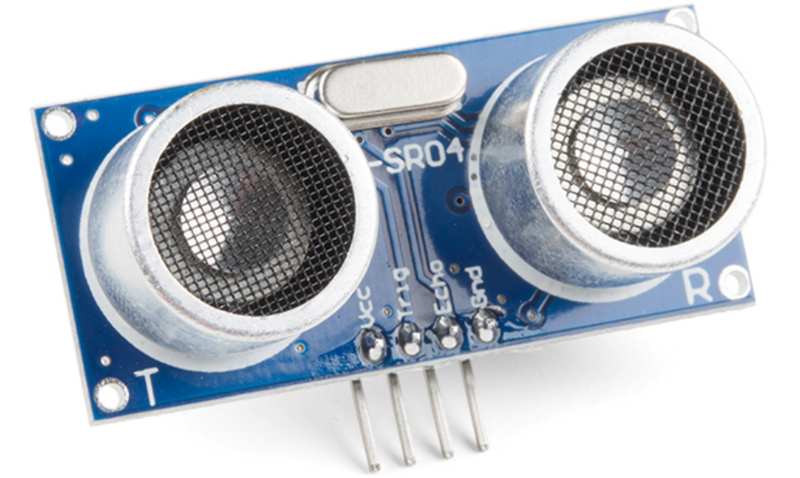
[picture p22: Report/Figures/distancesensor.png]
     % Adjust width as needed
    \caption{HC-SR04 Ultrasonic Ranging Module}
    \label{fig:distancesensor}
\end{figure}

As an extra feature, we decided to use two \textbf{HC-SR04} sensors for sensing proximity to objects. It operates by emitting an ultrasonic pulse from its transmitter and measuring the time it takes for the pulse to reflect off a nearby surface and return to the receiver. The module communicates via a simple TTL interface, requiring a 'trigger' signal to start the measurement and an 'echo' signal to indicate when the reflected pulse is received. By calculating the time interval between the trigger and echo signals, the distance to the object can be determined.

\

We decided to use timers and interrupt service routines to measure the time of this pulse. Specifically, we used the input capture mode, which would trigger on both rising and falling edges of the Echo signal, enabling precise capture of timer values at each transition. By handling these events in interrupt service routines, the CPU remained free to execute other tasks concurrently with the distance measurement process.

\

A code sample for the firmware implementation of input capture interrupt are shown in Listing \ref{lst:stm32_distancesensor_code} in the Appendix. More information about input capture mode and its implementation can be found on this site, \href{https://community.st.com/t5/stm32-mcus/how-to-use-the-input-capture-feature/ta-p/704161}{here}. If the module sensed a distance smaller than 30cm, a basic GPIO pin would be set low to communicate to the Arduino of this status.

\subsubsection{Color Sensing}
\label{sec:colorsensor}
\begin{figure}[H]
    \centering
    \setlength{\fboxsep}{0pt}%
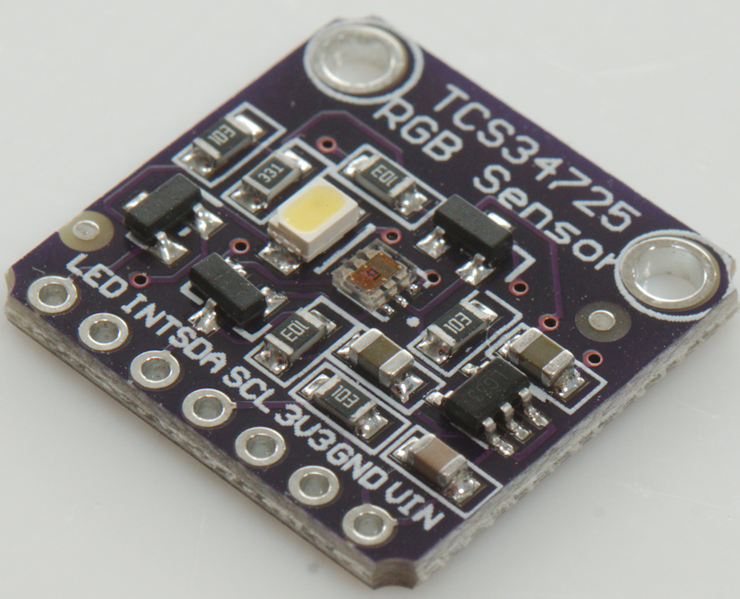
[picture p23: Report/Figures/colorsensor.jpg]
    \fbox{} % Adjust width as needed
    \caption{TCS34725 Light-to-Digital Sensor}
    \label{fig:colorsensor}
\end{figure}

We decided to integrate the \textbf{TCS34725} Color Sensor Module, responsible for detecting the color composition of a surface by measuring the intensity of red, green, blue, and clear light. It communicates via an I$^2$C interface, and was implemented on the \emph{STM32L051} microcontroller. The STM32 HAL libraries simplify I\textsuperscript{2}C communication, as demonstrated in Listing~\ref{lst:stm32_colorsensor_code}.

\

The \texttt{ColorSensor\_Handle} function is called within the main control loop. It reads the values from each color channel register (16 bits) and determines the most dominant color. If the red channel is the most prominent, the speaker is triggered to notify the user of the sensor's detection. When this would occur, a basic GPIO pin would be set low to communicate to the Arduino of this status.

\subsubsection{RFID Security System}
\label{sec:rfidsensor}
\begin{figure}[H]
    \centering
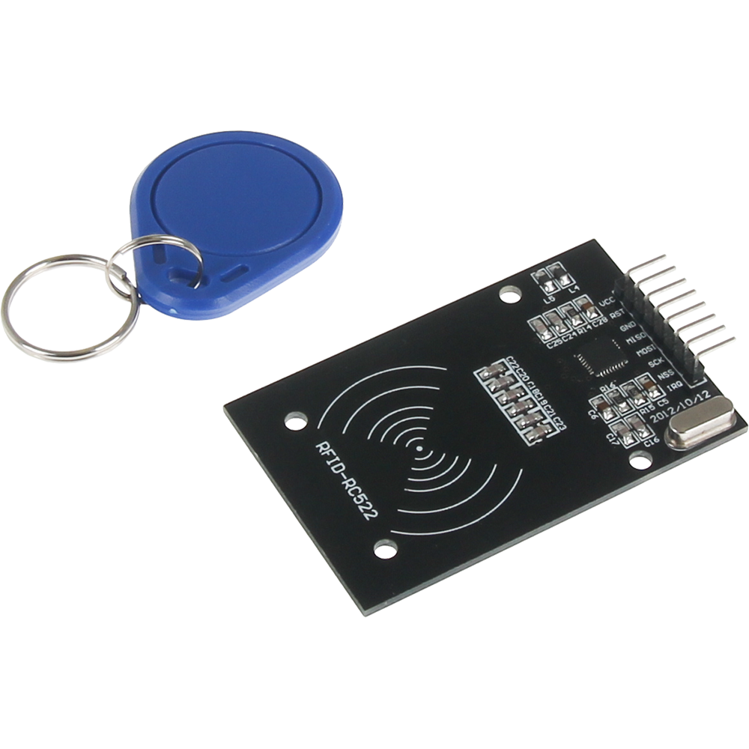
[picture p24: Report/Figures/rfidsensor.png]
     % Adjust width as needed
    \caption{RC522 Contactless Reader IC}
    \label{fig:rfidsensor}

\end{figure}

The \textbf{RC522} RFID Module was responsible for detecting and reading passive RFID tags using radio frequency communication at 13.56MHz. It operates over an SPI interface, allowing for fast and efficient data exchange with the \emph{STM32L051} microcontroller. When a tag enters the RF field generated by the module’s antenna, the RC522 initiates a handshake protocol and reads the tag’s unique identifier (UID) stored in its internal memory.

\

In the case where the correct RFID tag would be scanned, a basic GPIO pin would be set low and the speaker would be triggered to communicate to the Arduino of this status. The remaining logic specific to our application is shown in Listing \ref{lst:stm32_rfidsensor_code} in the Appendix.

\subsubsection{CEM-1302 Speaker/Buzzer}
\label{sec:speaker}
\begin{figure}[H]
    \centering
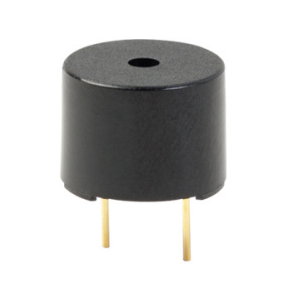
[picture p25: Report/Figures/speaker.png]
     % Adjust width as needed
    \caption{CEM-1302 Speaker/Buzzer}
    \label{fig:speaker}
\end{figure}

We used the CEM-1302 buzzer to indicate the following key events:
\begin{itemize}
    \item RFID: Indicating successful and unsuccessful RFID card scans
    \item Ultrasonic Sensor: Alerting when the distance between the robot and an object is too small
    \item Color Sensor: Signaling when the color sensor detects a predominantly red color
\end{itemize}

When any of these events occurred, the speaker would either beep, or stay on, depending on the scenario. Code for the setup can be seen in Listing \ref{lst:stm32_speaker_code}. The speaker was also developed on the \emph{STM32L051}, using a square wave PWM running at 2.048kHz. GPIO pins for these events were used to communicate with the Arduino Nano for simplicity and speed.

\subsection{Raspberry Pi Zero 2 W}

The \textbf{Raspberry Pi Zero 2 W} is an affordable single-board computer designed for
embedded systems and IoT applications. We leveraged its camera connector (CSI-2 interface)
to interface with a \textbf{Freenove 5MP Camera}, as well as its Wi-Fi capabilities to
wirelessly access it the \textbf{Raspberry Pi Connect} software.

\begin{figure}[H]
    \centering
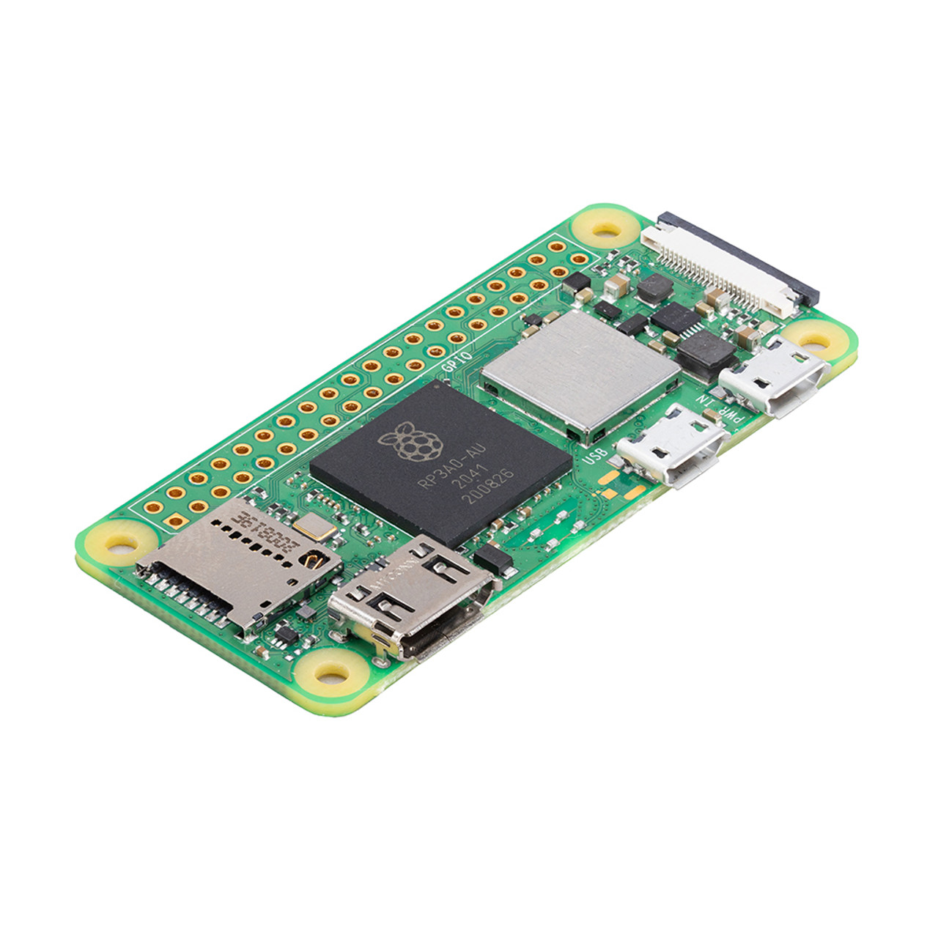
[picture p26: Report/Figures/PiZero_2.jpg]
    
    \caption{Raspberry Pi Zero 2 W}
    \label{fig:raspberrypi}
\end{figure}

\subsubsection{Camera App}

\begin{minipage}{\linewidth}
    We developed a \textbf{Python} application to display the live camera feed in a \textbf{Tkinter GUI} window,
    allowing the user to observe and record the operation of the robot. The user interface provided the ability to also
    take snapshots and store these in the \textbf{SD Card} storage. \\

    The live feed was largely a result of scheduling an update function with \textbf{Tkinter}'s \texttt{after(\dots)} method,
    which allowed us to sample camera frames at a rate of $20$ FPS. \\

    Since the \textbf{Raspberry Pi Zero 2 W} had power and performance constraints (i.e. $512$ MB of SDRAM),
    we ensured that the application was optimized for performance and iterated software versioning
    to minimize resource consumption. The camera was configured to capture frames at a resolution of $480$ pixels to account for this. \\
\end{minipage}

\begin{figure}[H]
    \centering
    
    \caption{PiCamera Application}
    \label{fig:camera_app}
\end{figure}

\begin{center}
    The class and methods for the camera display are shown in Listing \ref{lst:picamera_display_code} in the Appendix. \\
\end{center}

\begin{minipage}{\linewidth}
    Early on in development, we switched from the \textbf{Kivy} framework. This provided smoother animations, but rendering was
    hardware accelerated. We were unconfident with the \textbf{Raspberry Pi Zero 2 W}'s ability to provide adequate performance with this,
    and ported the application to the current implementation.
\end{minipage}

\subsubsection{AWS Bucket}

\begin{minipage}{\linewidth}
    Another constraint we considered during implementation was the inability to
    connect to the \textbf{Raspberry Pi} without powering on the robot. Having to access recording and snapshots
    would be quite cumbersome for the user. \\
\end{minipage}

\begin{figure}[H]
    \centering
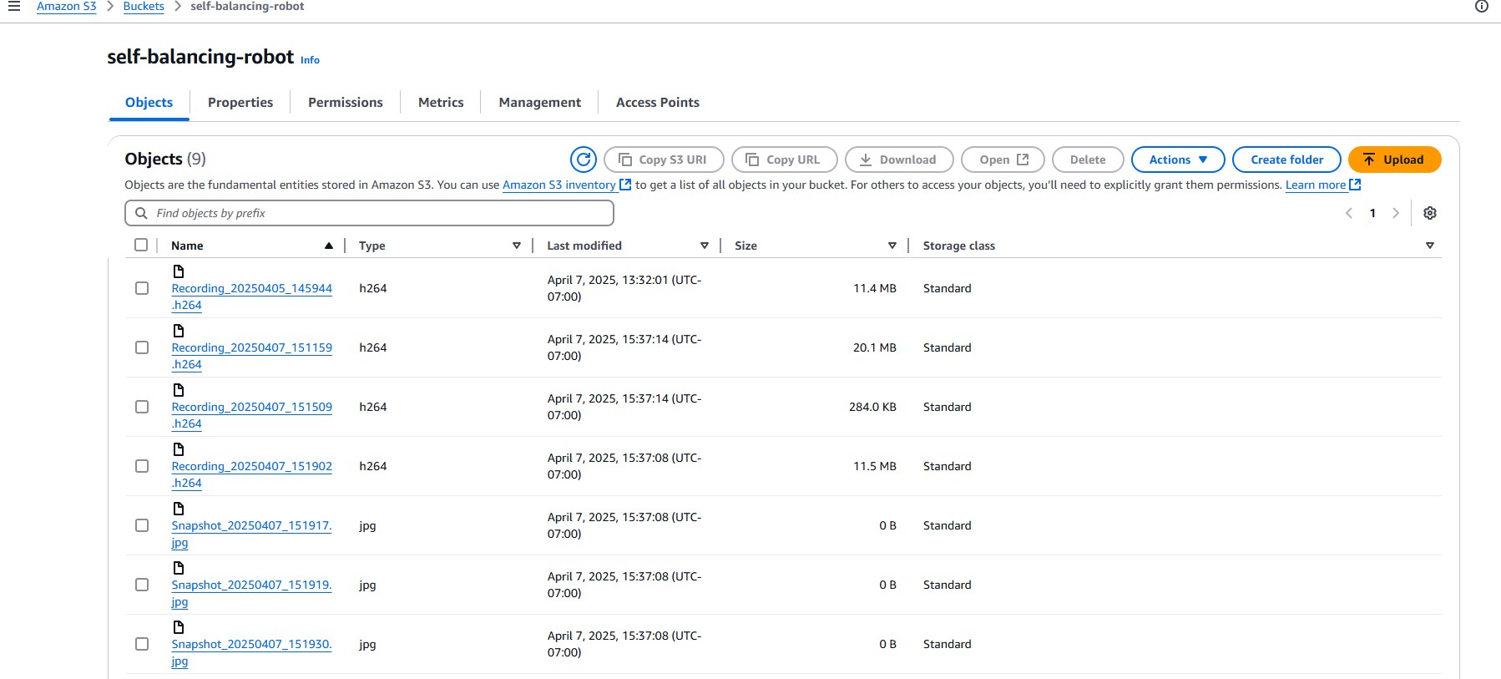
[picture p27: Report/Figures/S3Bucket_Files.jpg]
    
    \caption{AWS S3 Bucket}
    \label{fig:s3_bucket}
\end{figure}

\begin{minipage}{\linewidth}
    We created an \textbf{AWS S3 Bucket} and uploaded the camera recordings and snapshots during operation.
    The \textbf{Boto} package enabled us to implement this in our \textbf{Python} application by leveraging the \textbf{AWS SDK}.
    We were able to download these files from the \textbf{AWS S3 Bucket} to our local machine for offline access.
\end{minipage}

\section{Meeting Requirements}
\subsection{Verification}

\begin{minipage}{\linewidth}
    To evaluate the core functionality of the robot, we leveraged the \textbf{Serial} and \textbf{BLE} capability of the \textbf{Arduino} microcontroller to both observe and modify \textbf{PID} I/O signals. \\

    This was done to compare performance as we tweaked parameters. \\
\end{minipage}

\subsubsection{Angle Accuracy}

\begin{minipage}{\linewidth}
    Early on in development, we realized that accurate angle measurements were critical to the robot's ability to successfully
    balance itself. \\

    We developed a \textbf{Python} user interface to visualize the angle measurements from the \textbf{Arduino} in real-time,
    included in Listing \ref{lst:stripchart_code} in the Appendix. \\
\end{minipage}

\begin{figure}[H]
    \centering
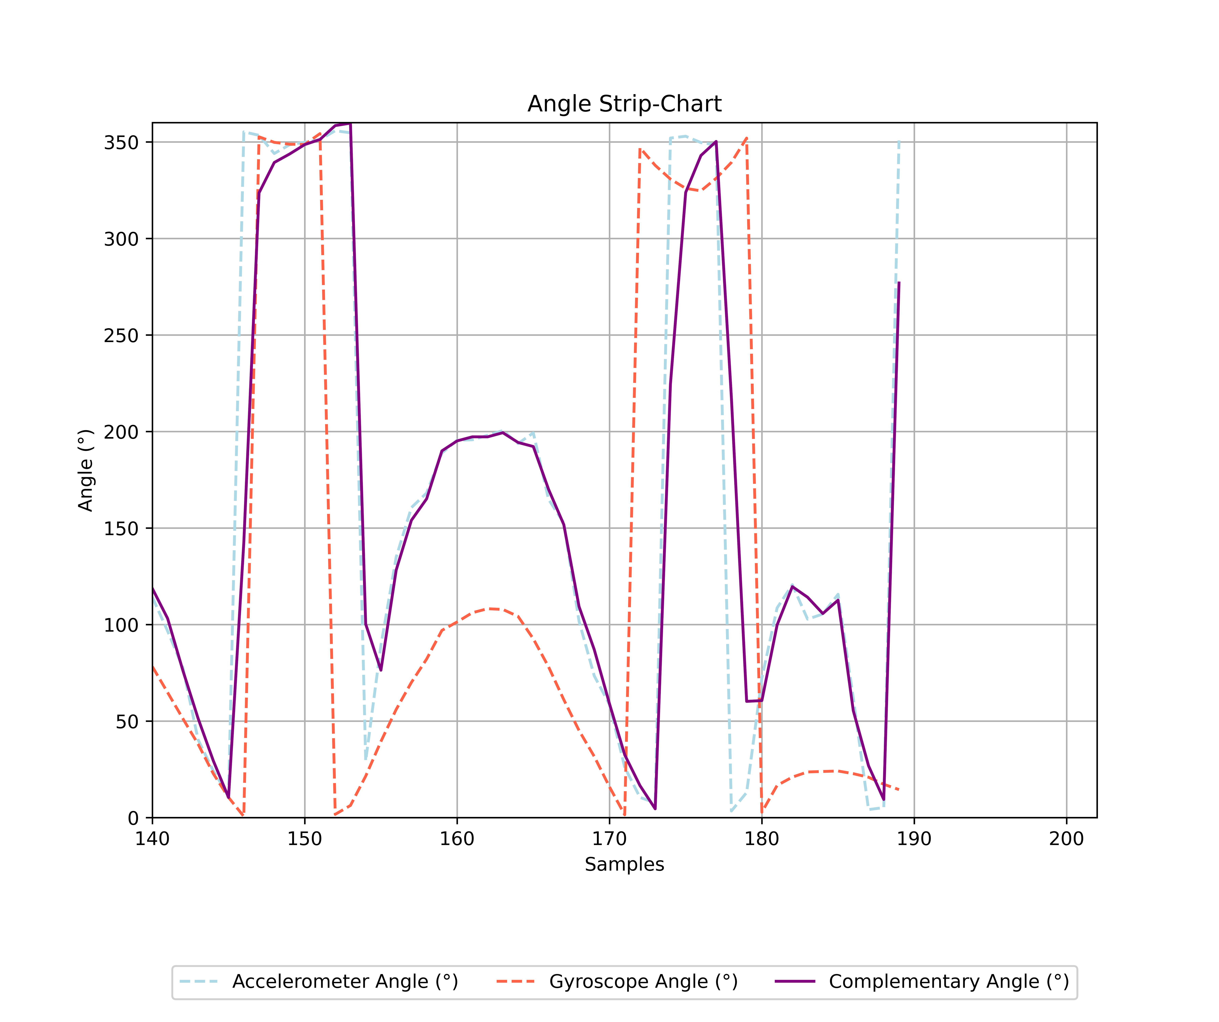
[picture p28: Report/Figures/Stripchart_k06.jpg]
    \fbox{}
    \caption{Angle Measurements (k = 0.6)}
    \label{fig:stripchart_k06}
\end{figure}

\begin{minipage}{\linewidth}
    As shown in the example in Figure~\ref{fig:stripchart_k06}, we rotated the \textbf{Arduino} microcontroller within a predefined angle range
    and observed the complementary filter's performance with a given $k$ value. \\

    From saving and comparing these logs, we observed trends in the
    angle measurements from the accelerometer and gyroscope. This enabled us to optimize the benefits of both sensors and
    was critical in ensuring that we were able to balance the robot successfully.
\end{minipage}

\subsubsection{Model Parameters}

\begin{minipage}{\linewidth}
    Similarly, we developed a debugging tool in the \textbf{Arduino} firmware to tune \textbf{PID} parameters during operation (\textbf{FR1}, \textbf{FR6}).
    The source code for this is shown in Listing \ref{lst:arduino_ble_tuning_code} in the Appendix. \\
\end{minipage}

\begin{minipage}{\linewidth}
    When we were confident in the actual system level logic, we used the \textbf{BLE} capabilities to tune the following parameters. \\
\end{minipage}

\begin{itemize}
    \item PID Gains ($K_p$, $K_i$, $K_d$)
    \item Complementary Filter Weight ($k$)
    \item Setpoint Angle ($\theta_{set}$)
\end{itemize}

\begin{minipage}{\linewidth}
    During operation, we observed the effect of increasing / decreasing each of these on meeting the balancing requirements from
    Table~\ref{tab:functional_requirements}. \\
\end{minipage}

\begin{table}[H]
    \centering
    \renewcommand{\arraystretch}{1.3}
    \begin{tabularx}{\textwidth}{|c|X|X|}
        \hline
        \textbf{Parameter} & \textbf{Behavior When Increased} & \textbf{Behavior When Decreased} \\
        \hline
        $K_p$ & Undershoot & Overshoot, Tipping over When $K_p$ Too High .\\
        \hline
        $K_i$ & Drifting, Undershoot & Degraded Stability, Oscillates Near Reference Angle. \\
        \hline
        $K_d$ & Drifting, Overshoot & Oscillates Near Reference Angle \\
        \hline
        $k$ & Faster, Smooth Response. Accumulates Drift. & Increases Noise Influence, Experiences Jitter. No Drift. \\
        \hline
        $\theta_{set}$ & Drifting in Forward Direction. & Drifting in Backward Direction. \\
        \hline
    \end{tabularx}
    \caption{PID Parameters and System Behavior}
    \label{tab:parameter_behavior}
\end{table}

\subsubsection{Movement Implementation}
To verify that the movement met the requirements outlined in \textbf{PR5},
we tested the robot's ability to respond accurately to directional commands sent via the \textbf{BLE} interface.
Using a mobile device, we issued \textbf{FORWARD, BACKWARD, LEFT, RIGHT} commands while observing the robot's response in real time.
The robot successfully executed each command within the $5$ s time interval,
while maintaining balance, demonstrating reliable communication and precise motor control.
This confirmed that the \textbf{BLE} movement functionality met the performance expectations specified in the requirement.

\subsubsection{Remaining Requirements}
To verify the remaining requirements not covered above, we relied on a combination of simple tools and observation.
For distance and size-related measurements, we used rulers to confirm dimensions and movement ranges.
Timing-sensitive behaviors was evaluated with internal timers and debug outputs via \textbf{USART}. We used these to ensure response times and delays were adequate.
In cases where quantitative measurement was unnecessary or impractical, we used visual observation to confirm correct operation.
These methods provided sufficient confidence that the robot met the functional and performance criteria across all remaining requirements.

\subsection{Validation}

\subsubsection{User Acceptance Testing (UAT)}

\begin{minipage}{\linewidth}
    Similar to the software development cycle, we tested the integration of both core and extra features
    with critical examination from team stakeholders. \\

    We delegated this for there to be an owner responsible for implementation, but another team member who set the requirements for success in Table~\ref{tab:functional_requirements} and Table~\ref{tab:performance_requirements}. \\

    Looking at the ability to balance and move the robot, the Modeling Lead was the UAT lead in providing feedback for firmware implementation, whereas the Firmware \& Extra Features Leads provided feedback on current parameters. \\
\end{minipage}

\subsubsection{Balancing Criteria}
\begin{minipage}{\linewidth}
    To observe the borders of stability (i.e. analogous to edge-case testing), we placed the robot on the lab floor and observed its ability to balance (without external assistance) for $1$ minute (\textbf{FR1}). \\

    A ruler was placed on the ground to measure drift accumulation (\textbf{PR2}). Once the robot
    was able to maintain balance $> 5$ minutes and remained relatively
    stationary (i.e. drifting $< 5$ cm), we unanimously agreed that results indicated that we met the balancing
    requirement. \\
\end{minipage}\vspace{0.5mm}

\subsubsection{Angle Management}

\begin{minipage}{\linewidth}
    To test angle management (i.e. resilience to external force), we introduced noise to the system.
    We applied a force to the top of the pendulum to tilt
    the robot $\sim 15 \deg$ and observed whether it could recover without
    tipping over (\textbf{PR1}). \\

    The robot successfully recovered from angular tilts $\leq 20 \deg$
    without oscillation. However, when the tilt angle $> 20 \deg$, we observed that it was
    unable to recover from the disturbance. Observing this border of stability gave us understanding
    of the system behavior while making us confident that we met the set requirement of angle management
    within the expected operating range.\\
\end{minipage}

\subsubsection{STM32 Sensors}

\begin{minipage}{\linewidth}
    We approached the integration of environmental response as an enhancement of existing core functionality.
    We should be able to meet all existing requirements, while enhancing the user experience. When testing the utility of
    the \textbf{HC-SR04} distance sensor and \textbf{TCS34725} color sensor, we prioritized the following main criteria:
    \begin{itemize}
        \item Balancing should be unaffected by the addition of sensors (i.e.~\textbf{PR1}, \textbf{PR2})
        \item Driver should be able to navigate the robot from A to B within a reasonable time (i.e.~\textbf{PR3}, \textbf{PR5}).
        \item The robot should not hit any obstacles while moving (i.e.~\textbf{PR6}).
    \end{itemize}

    These are inherently included in the requirements from Table~\ref{tab:functional_requirements} and Table~\ref{tab:performance_requirements}.
    However, we wanted to ensure that we could compare the ability to meet each of these both before / after feature integration,
    and ensure that we either avoid or reduce performance degradation. \\

    Once we observed that this (qualitatively) made it easier to navigate the robot and meet the relevant performance requirements, we
    labeled the feature as a success. \\
\end{minipage}

\subsubsection{Secure Authentication}

\begin{minipage}{\linewidth}
    Similarly, the addition of the \textbf{RC522} RFID module and \textbf{BLE} authentication were designed to enhance the security of the robot.
    These actually were designed to make it more difficult for user onboarding in a sense. However, we wanted to ensure that access was as simple for the
    intended user, while being as difficult as possible for an unauthorized user. \\

    The \textbf{Robot Driver App} was appropriately designed such that other team members could easily onboard themselves to the robot, without knowing
    that the intended application handled the authentication process in the background. The Firmware Lead was responsible for this,
    and observed team member onboarding difficulty as a success metric. \\

    To ensure security was prioritized, we performed edge-case testing in which either the \textbf{BLE} connection was interrupted or the
    \textbf{RC522} RFID module was disconnected. We observed that the robot prevented access under these conditions, but could unconditionally recover
    if they were reconnected. \\
\end{minipage}

\subsubsection{Camera File Storage}

\begin{minipage}{\linewidth}
    We struggled the most with the \textbf{Raspberry Pi Zero 2 W} camera feed. It was straightforward to meet the success criteria of being able to record at $1$ FPS and display the live feed.
    We were also able to succesfully store images/videos to the \textbf{SD Card} storage. However,
    (an implied) success criteria entailed the user being able to successfully complete the end-to-end process of accessing the camera feed and downloading the images/videos from the \textbf{AWS S3 Bucket}. \\

    We had to perform this test under the condition that the robot was powered off in the downloading stage. Once this was met, the feature was (tentatively) labeled as a success. \\
\end{minipage}

\section{Conclusion}

\begin{minipage}{\linewidth}
    The implementation of the PID controller was effective and enabled the robot to
    balance with reasonable resistance to external disturbances. However, one
    improvement would be to utilize an encoder and implement an additional,
    cascaded PID controller. This could help reduce oscillations and improve the
    robot's ability to remain stationary. It may also enhance the angle
    management. Since the current system requires a relatively high $K_i$ term to
    maintain balance, it has degraded stability under significant external
    disturbances. By introducing a cascaded PID controller, the $K_i$ term in the main
    controller could be reduced, leading to improved stability and better angle
    management. \\

    In terms of structural design, we raised the third layer to increase the
    linearity of the system's step response within its controllable region. While
    this improves linearity, it also narrows the linear region and makes the robot
    more prone to external disturbances. One possible improvement is to replace the
    current motors with ones that have less mechanical slack, which would provide a
    more responsive system. This would allow us to lower the third layer, enhancing
    angle management while maintaining linear behavior. \\
\end{minipage}

\subsection{Future Improvements}

\begin{minipage}{\linewidth}
    For future revisions, especially related to control systems, we have a few key takeaways.
        \begin{itemize}
            \item \textbf{Keep the PID control code as simple and straightforward as possible.}
                \begin{itemize}
                    \item Adding excessive logic, layers of filtering, and unnecessary conditions introduced both complexity and instability in our system, which made tuning more difficult.
                \end{itemize}

            \item \textbf{Avoid tuning the PID controller until key modules for background calculations are integrated}.
                \begin{itemize}
                    \item Adding / removing modules can shift timing and alter the effective control behavior, which would lead to a vicious cycle of re-tuning.
                    \item Introducing deliberate delays can help simulate sensor acquisition timing during early development.
                \end{itemize}

            \item \textbf{Finalize the robot's physical design before tuning the controller (i.e.~mass distribution, wheelbase, and component placement).}
                \begin{itemize}
                    \item Significant changes to the hardware likely affect system dynamics and invalidate earlier tuning efforts (i.e. leading to cyclical controller tuning).
                \end{itemize}

            \item \textbf{Use real-time plotting / data logging to observe variables such as sensor readings, control output, and error values.}
                \begin{itemize}
                    \item This helps in diagnosing control issues and speeding up the tuning process.
                    \item We originally planned on addressing this with the \textbf{Raspberry Pi} serial interface, but due to time constraints, were unable to meet the necessary acceptance criteria to use this and enhance our system.
                \end{itemize}

            \item \textbf{Avoid over-relying on simulation unless the model is very accurate.}
                \begin{itemize}
                    \item Physical systems often behave unpredictably due to noise, friction, and delays, which are difficult to capture in simulation.
                \end{itemize}

            \item \textbf{Make safety a priority when testing control systems.}
                \begin{itemize}
                    \item Starting with lower gains and gradually increasing them, especially on inherently unstable systems like the self-balancing robot, helps improve performance without the risk of instability.
                \end{itemize}

            \item \textbf{Seemlessly integrate the security experience in the software tools.}
                \begin{itemize}
                    \item We started enhancing the security of the robot very late during development.
                    \item Implementing a \textbf{BLE} pairing code was an idea we toyed with throughout this 12-week project. However, we were inspired to implement the firmware layer when we realized our robot was vulnerable to unauthorized access.
                    \item Another addition we'd have added given $\sim 1$ week of development would be to implement a password in the \textbf{Robot Driver App} to add another layer of security (i.e. via software).
                \end{itemize}
        \end{itemize}
    \end{minipage}

\section{References}
\printbibliography[heading=none]

\section{Appendices}

\subsection{Appendix: Budget}

\begin{figure}[H]
    \centering
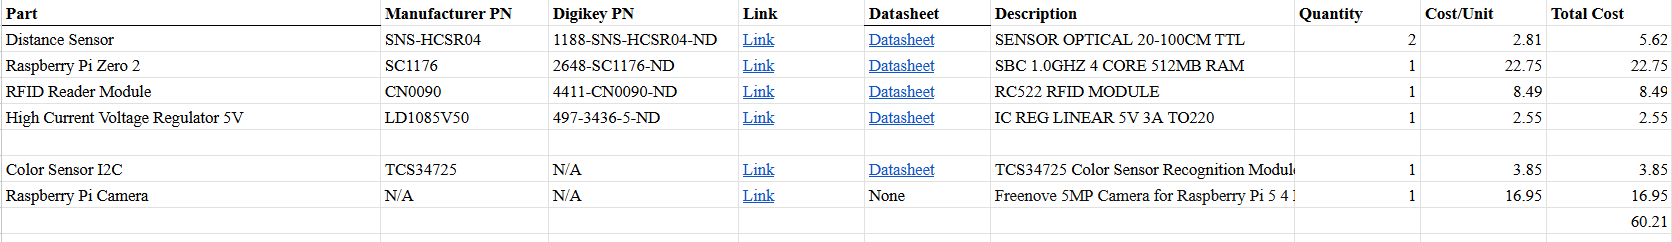
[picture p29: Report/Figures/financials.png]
    {\setlength{\fboxsep}{0pt}\fbox{}}
    \caption{Extra Features Financial Summary}
    \label{fig:financials}
\end{figure}

\subsection{Appendix: Technical Calculations and Simulations}

\begin{table}[H]
    \centering
    \label{tab:imu_sensors}
    \begin{tabularx}{\textwidth}{|l|X|X|}
    \hline
    \textbf{Sensor} & \textbf{Pros} & \textbf{Cons} \\
    \hline
    \textbf{Accelerometer} &
    \begin{itemize}
        \item accurate gravitational readings
        \item zero-mean noise
    \end{itemize} &
    \begin{itemize}
        \item high noise variance (especially with motor vibrations)
    \end{itemize} \\
    \hline
    \textbf{Gyroscope} &
    \begin{itemize}
        \item lower noise over short time periods
    \end{itemize} &
    \begin{itemize}
        \item accumulates bias over time
    \end{itemize} \\
    \hline
    \end{tabularx}
    \caption{IMU Sensors: Pros and Cons}
\end{table}

% \subsection{Appendix: Drawings, Schematics, and Blueprints}
\subsection{Appendix: Datasheets / Product Specifications}
Supporting Datasheets and Technical Documentation for Core Features (does not include battery related components, mechanical components, or generic electrical components):

\begin{enumerate}
    \item \href{https://docs.arduino.cc/resources/datasheets/ABX00069-datasheet.pdf}{Arduino Nano 33 IoT (ABX00069) Datasheet}
    \item \href{https://www.pololu.com/file/0J1736/pololu-37d-metal-gearmotors-rev-1-2.pdf}{Pololu 37D Metal Gearmotor Specifications}
    \item \href{https://www.ti.com/lit/ds/symlink/drv8833.pdf?ts=1743785858420}{Texas Instruments DRV8833 Dual H-Bridge Motor Driver Datasheet}
\end{enumerate}

\

Supporting Datasheets and Technical Documentation for Additional Features:
\begin{enumerate}
    \item \href{https://cdn.sparkfun.com/datasheets/Sensors/Proximity/HCSR04.pdf}{HC-SR04 Ultrasonic Distance Sensor}
    \item \href{https://cdn-shop.adafruit.com/datasheets/TCS34725.pdf}{TCS34725 Color Sensor}
    \item \href{https://datasheets.raspberrypi.com/rpizero2/raspberry-pi-zero-2-w-product-brief.pdf}{Raspberry Pi Zero 2 W}
    \item \href{https://mm.digikey.com/Volume0/opasdata/d220001/medias/docus/60/CN0090%20DATASHEET.pdf}{CN0090 Accelerometer Board}
    \item \href{https://www.st.com/content/ccc/resource/technical/document/datasheet/d3/84/d5/f6/3c/23/40/7b/CD00001883.pdf/files/CD00001883.pdf/jcr:content/translations/en.CD000018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}{L293D Motor Driver IC}
    \item \href{https://store.freenove.com/products/fnk0056}{Freenove 5MP Camera (FNK0056)}
    \item \href{https://www.sameskydevices.com/product/resource/cem-1203-42-.pdf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}{CEM-1302 Speaker/Buzzer}
\end{enumerate}
%\subsection{Appendix: Relevant Industry Standards and Regulations Used}
% \subsection{Appendix: Prototypes}

\subsection{Appendix: Source Code}

\begin{lstlisting}[caption={Source Code : Arduino IMU Complementary Filter}, label={lst:arduino_angle_code}]
ANGLES Angles = {0, 0, 0}; // Accelerometer, Gyroscope, Complementary
void getAngles(ANGLES &Angles) {
  float currAccel, currGyro, currComplementary;
  float sampleTime;

  if (!IMU.gyroscopeAvailable()) return;
  IMU.readGyroscope(gx, gy, gz);

  if (!IMU.accelerationAvailable()) return;
  IMU.readAcceleration(ax, ay, az);

  currAccel = atan2(az, ay) * (180 / PI);
  currAccel = (currAccel - 90) + ACCELEROMETER_OFFSET;

  sampleTime = 1.0 / IMU.gyroscopeSampleRate();

  currGyro = prevGyro + gx * sampleTime;

  prevAngle = prevComplementary;
  currComplementary = k * (prevComplementary + gx * sampleTime) + (1 - k) * currAccel;

  /* Update Time Variables */
  t_n = millis(); // Current Time in Milliseconds
  dt = (t_n - t_n1) / 1000.0; // Time Difference in Seconds
  t_n1 = t_n; // Assign Current Time to Previous Time

  /* Update Angles */
  Angles.Accelerometer = currAccel;
  Angles.Gyroscope = currGyro;
  Angles.Complementary = currComplementary;

  /* Assign Previous Angles */
  prevGyro = currGyro;
  prevComplementary = currComplementary;
}
\end{lstlisting}

\begin{lstlisting}[caption={Source Code : Arduino PID Controller}, label={lst:arduino_pid_code}]
void balanceRobot(int bleDirection) {
    // Get Measured Angle
    measuredAngle = Angles.Complementary; // Complementary Filter
    errorAngle = setpointAngle - measuredAngle; // e_t = r_t - y_t
    errorDifference = (errorAngle - prevErrorAngle) / dt; // e_t - e_(t-1) / dt
    errorAccumulation += (errorAngle * dt);

    // Reset Accumulated Error Value $\sum$e_t
    if (digitalRead(DISABLE_INTEGRAL_BUTTON) == LOW) errorAccumulation = 0;

    // Calculate Control Signal : u_t = Kp * e_t + Ki * $\sum$e_t + Kd * (e_t - e_(t-1) / dt)
    u_t = (Kp * errorAngle) + (Ki * errorAccumulation) + (Kd * errorDifference);
    drive(u_t, errorAngle);

    prevErrorAngle = errorAngle; // Update Previous Error Value
    return;
}
\end{lstlisting}

\begin{lstlisting}[caption={Source Code : Arduino Motor Driver}, label={lst:arduino_pwm_code}]
/*
 * Fast Decay: Hold Primary Input at PWM Duty Cycle, Secondary Input Low.
 */
void moveFastDecay(XIN &motor, DirPWM dir, float dutyCycle) {
    if (dir == CW) {
        motor.Pin1->write(dutyCycle);
        motor.Pin2->write(0);
    } else if (dir == CCW) {
        motor.Pin1->write(0);
        motor.Pin2->write(dutyCycle);
    }
}

/*
 * Slow Decay: Hold Primary Input High, Secondary Input at PWM Duty Cycle.
 */
void moveSlowDecay(XIN &motor, DirPWM dir, float dutyCycle) {
    if (dir == CW) {
        motor.Pin1->write(1);
        motor.Pin2->write(1-dutyCycle);
    } else if (dir == CCW) {
        motor.Pin1->write(1-dutyCycle);
        motor.Pin2->write(1);
    }
}
\end{lstlisting}

\begin{lstlisting}[caption={Source Code : Arduino Movement Statemachine}, label={lst:arduino_movement_code}]
void drive(float u_t, float errorAngle) {
    currDutyCycle = normalizePWM(u_t, 0);

    if (millis() - startTime >= 1500) {
        startTime = currTime; // Reset Start Time
        setpointAngle = SETPOINT_0;
        bleDirection = IDLE; // Stop Robot
    }

    if (redAlert) {
        startTime = currTime; // Reset Start Time
        setpointAngle = SETPOINT_0 + 1.5 * ANGLE_TILT;
        bleDirection = REVERSE;
    }

    switch (bleDirection) {
        case FORWARD:
            if (forwardAlert) setpointAngle = SETPOINT_0 + 0.5 * ANGLE_TILT;

            if (u_t > 0) moveForward(currDutyCycle);
            else moveReverse(currDutyCycle);
        break;
        case REVERSE:
            if (reverseAlert) setpointAngle = SETPOINT_0 - ANGLE_TILT;

            if (u_t > 0) moveForward(currDutyCycle);
            else moveReverse(currDutyCycle);
        break;
        case LEFT:
            if ((directionCount++ % 3 == 0) || (abs(errorAngle) > MAX_ERR_ANGLE)) {
                if (u_t > 0) moveForward(currDutyCycle);
                else moveReverse(currDutyCycle);
            } else {
                turnLeft(currDutyCycle, 0.6);
            }
        break;
        case RIGHT:
            if ((directionCount++ % 3 == 0) || (abs(errorAngle) > MAX_ERR_ANGLE)) {
                if (u_t > 0) moveForward(currDutyCycle);
                else moveReverse(currDutyCycle);
            } else {
                turnRight(currDutyCycle, 0.5);
            }
        break;
        default:
            if (u_t > 0) moveForward(currDutyCycle);
            else moveReverse(currDutyCycle);
        break;
    }
    return;
}
\end{lstlisting}
\begin{lstlisting}[caption={Source Code : Arduino BLE Functionality}, label={lst:arduino_ble_code}]
void setupBLE() {
  pinMode(LED_BUILTIN, OUTPUT); // Init Built-in LED to Indicate Connection Status

  if (!BLE.begin()) {
    Serial1.println("Starting BLE Failed!");
    while (1);
  }

  // Set Local Name and Device Name
  BLE.setLocalName("WALL-E");
  BLE.setDeviceName("WALL-E");

  BLE.setAdvertisedService(customService);
  customService.addCharacteristic(customCharacteristic);  // Add the Characteristic to the Service
  BLE.addService(customService); // Add the Service to the BLE Device

  // Callback Event Handlers
  BLE.setEventHandler(BLEConnected, connectBLE);
  BLE.setEventHandler(BLEDisconnected, disconnectBLE);
  customCharacteristic.setEventHandler(BLEWritten, rxBLE);

  BLE.advertise(); // Advertising the BLE Device

  while (!BLE.connected()) BLE.poll(); // Wait for Connection
  customCharacteristic.writeValue("Enter Code:"); // Send BLE Prompt
}

void connectBLE(BLEDevice central) {
  digitalWrite(LED_BUILTIN, HIGH);
  isPromptedBLE = false; // Reset BLE Prompt Flag
}

void disconnectBLE(BLEDevice central) {
  digitalWrite(LED_BUILTIN, LOW);
  isAuthenticated = false; // Reset Authentication Status
}

void authBLE() {
  if (strcmp(buffBLE, CODE) == 0) {
    isAuthenticated = true;
    customCharacteristic.writeValue("Auth Success!");
    isAuthenticated = true; // Set Authentication Status
  } else {
    customCharacteristic.writeValue("Auth Fail!");
    BLE.disconnect(); // Disconnect if Authentication Fails
  }

}

void rxBLE(BLEDevice central, BLECharacteristic characteristic) {
  int length = characteristic.valueLength();
  const unsigned char* receivedData = characteristic.value();

  memcpy(buffBLE, receivedData, length);
  buffBLE[length] = '\0'; // Null-Terminated

  if (isAuthenticated) {
    // updateParamBLE(buffBLE); // Update PID Parameters Based On BLE Input
    changeDirection(buffBLE); // Change Direction Based On BLE Input
  } else {
    authBLE(); // Authenticate Device
  }
  return;
}
\end{lstlisting}

\begin{lstlisting}[caption={Source Code : Arduino BLE Parameter Updates}, label={lst:arduino_ble_tuning_code}]
void updateParamBLE(const char* bleBuff) {
  char paramType[STD_BUFFSIZE] = {0};
  char valueStr[STD_BUFFSIZE] = {0};
  float newValue = 0.0f;

  char returnStr[STD_BUFFSIZE] = {0};

  char cmd[STD_BUFFSIZE] = {0};
  strcpy(cmd, bleBuff); // Copy Command to Local Buffer

  int start = 0;
  while ((cmd[start] == ' ') || (cmd[start] == '\t')) start++; // Skip Leading Whitespace

  if (
    strncmp(&cmd[start], "k=", 2) == 0 ||
    strncmp(&cmd[start], "set=", 4) == 0 ||
    strncmp(&cmd[start], "Kp=", 3) == 0 ||
    strncmp(&cmd[start], "Ki=", 3) == 0 ||
    strncmp(&cmd[start], "Kd=", 3) == 0
  ) {
    char* equalsPos = strchr(&cmd[start], '='); // Find '=' Position
    if (!equalsPos) return;

    int paramLength = equalsPos - &cmd[start]; // Length of Parameter Name
    strncpy(paramType, &cmd[start], paramLength); // Copy Parameter Name
    paramType[paramLength] = '\0'; // Null-Termination

    strcpy(valueStr, equalsPos + 1); // Copy Value String
    newValue = atof(valueStr); // Convert Value String to Float

    if (strcmp(paramType, "k") == 0) k = newValue;
    else if (strcmp(paramType, "set") == 0) SETPOINT_0 = newValue;
    else if (strcmp(paramType, "Kp") == 0) Kp = newValue;
    else if (strcmp(paramType, "Ki") == 0) Ki = newValue;
    else if (strcmp(paramType, "Kd") == 0) Kd = newValue;
    else return; // Invalid Command

    sprintf(returnStr, "NewVal: %s=%s", paramType, valueStr);
    customCharacteristic.writeValue(returnStr);
  }
  return; // Exit Function
}
\end{lstlisting}

\begin{lstlisting}[caption={Source Code : STM32 HC-SR04 Firmware}, label={lst:stm32_distancesensor_code}]
void DistanceSensor_InputCaptureInterrupt(distancesensor* sensor)
{
    if (HAL_GPIO_ReadPin(sensor->icGPIOPort, sensor->icGPIOPin)) {
        sensor->IC_Value1 = HAL_TIM_ReadCapturedValue(sensor->timer, TIM_CHANNEL_1); // First rising edge
        HAL_TIM_PWM_Stop(sensor->timer, TIM_CHANNEL_2);
    }
    else {
        sensor->IC_Value2 = HAL_TIM_ReadCapturedValue(sensor->timer, TIM_CHANNEL_1); // Second rising edge
        if (sensor->IC_Value2 > sensor->IC_Value1) {
            sensor->timeDifference = sensor->IC_Value2 - sensor->IC_Value1;
        }
        else {
            sensor->timeDifference = (TIM_PERIOD + 1 - sensor->IC_Value1) + sensor->IC_Value2; // Handle overflow
        }

        HAL_TIM_PWM_Start(sensor->timer, TIM_CHANNEL_2);
        __HAL_TIM_SetCounter(sensor->timer, 65535);

        DistanceSensor_Handle(sensor);
    }
}

// On main.c:

void HAL_TIM_IC_CaptureCallback(TIM_HandleTypeDef *htim) {
    if (htim->Instance == TIM21) {
		DistanceSensor_InputCaptureInterrupt(&Front);
	}
	else if (htim->Instance == TIM22) {
		DistanceSensor_InputCaptureInterrupt(&Back);
	}

}
\end{lstlisting}

\begin{lstlisting}[caption={Source Code : STM32 TCS34725 Firmware}, label={lst:stm32_colorsensor_code}]
#include "colorsensor.h"

#define TCS3472_SLAVE_ADDRESS 0x29 << 1
#define TCS3472_EXPECTED_ID 0x44

#define TCS3472_ID_REG 0x12

#define TCS3472_WTIME_REG 0x03
#define TCS3472_ATIME_REG 0xF6
#define TCS3472_ENABLE_REG 0x00

#define TCS3472_CDATAL_REG 0x14
#define TCS3472_RDATAL_REG 0x16
#define TCS3472_GDATAL_REG 0x18
#define TCS3472_BDATAL_REG 0x1A

extern speaker Speaker;

void ColorSensor_Init(colorsensor* sensor, I2C_HandleTypeDef* i2c_handle) {
    sensor->i2c = i2c_handle;
    sensor->slave_address = TCS3472_SLAVE_ADDRESS;

    memset(sensor->rgb_data, 0, sizeof(sensor->rgb_data));  // Clear RGB data
    sensor->enabled = true;
    sensor->count = 0;

    // Define initialization sequence
    uint8_t init_data[][2] = {
        { TCS3472_WTIME_REG  | 0x80, 0xFF },  // Wait time
        { TCS3472_ATIME_REG  | 0x80, 0xFF },  // Integration time
        { TCS3472_ENABLE_REG | 0x80, 0x0B },   // Power ON & enable RGBC
    };

    // Loop through initialization commands and send them
    for (size_t i = 0; i < sizeof(init_data) / sizeof(init_data[0]); i++) {
        if (HAL_I2C_Master_Transmit(sensor->i2c, sensor->slave_address, init_data[i], 2, HAL_MAX_DELAY) != HAL_OK)
        	while(1);
    }

    HAL_GPIO_WritePin(COLOR_SENSOR_STATUS_GPIO_Port, COLOR_SENSOR_STATUS_Pin, GPIO_PIN_SET);
}

void ColorSensor_EnableStatus(colorsensor* sensor, bool enable)
{
	sensor->enabled = enable;
}

uint16_t ColorSensor_Read16(colorsensor* sensor, uint8_t reg) {
    uint8_t buffer[2];
    uint8_t command = reg | 0xA0;  // Add auto-increment bit

    // Send register address
    if (HAL_I2C_Master_Transmit(sensor->i2c, sensor->slave_address, &command, 1, HAL_MAX_DELAY) != HAL_OK) {
        return 0; // Handle error
    }

    // Read 2 bytes from the sensor
    if (HAL_I2C_Master_Receive(sensor->i2c, sensor->slave_address, buffer, 2, HAL_MAX_DELAY) != HAL_OK) {
        return 0; // Handle error
    }

    // Combine two bytes into a 16-bit value (LSB first)
    return (uint16_t)(buffer[0] | (buffer[1] << 8));
}

void ColorSensor_ReadAll(colorsensor* sensor) {
    sensor->rgb_data[0] = ColorSensor_Read16(sensor, TCS3472_CDATAL_REG); // TCS3472_CDATAL
    sensor->rgb_data[1]   = ColorSensor_Read16(sensor, TCS3472_RDATAL_REG); // TCS3472_RDATAL
    sensor->rgb_data[2] = ColorSensor_Read16(sensor, TCS3472_GDATAL_REG); // TCS3472_GDATAL
    sensor->rgb_data[3]  = ColorSensor_Read16(sensor, TCS3472_BDATAL_REG); // TCS3472_BDATAL
}

color ColorSensor_CalculateColor(colorsensor* sensor)
{
	uint16_t max_val = sensor->rgb_data[1];
	color detected_color = RED;

	if (sensor->rgb_data[2] > max_val) detected_color = GREEN;
	if (sensor->rgb_data[3] > max_val) detected_color = BLUE;

	return detected_color;
}

void ColorSensor_Handle(colorsensor* sensor)
{
	ColorSensor_ReadAll(sensor);
	color detected_color = ColorSensor_CalculateColor(sensor);

	if (detected_color == RED)
	{
		HAL_GPIO_WritePin(COLOR_SENSOR_STATUS_GPIO_Port, COLOR_SENSOR_STATUS_Pin, GPIO_PIN_RESET);
		if (!Speaker.hasFault)
			Speaker_Start(&Speaker, COLOR_SENSOR_ID);
	}
	else
	{
		HAL_GPIO_WritePin(COLOR_SENSOR_STATUS_GPIO_Port, COLOR_SENSOR_STATUS_Pin, GPIO_PIN_SET);
		if (Speaker.hasFault)
			Speaker_Stop(&Speaker, COLOR_SENSOR_ID);
	}

}
\end{lstlisting}

\begin{lstlisting}[caption={Source Code : STM32 RC522 Firmware}, label={lst:stm32_rfidsensor_code}]
#include "rfid.h"

#include "speaker.h"

#define SERIALNUM_1_IDLE 32

#define SERIALNUM_0_CORRECT_CARD 170
#define SERIALNUM_1_CORRECT_CARD 205
#define SERIALNUM_2_CORRECT_CARD 47
#define SERIALNUM_3_CORRECT_CARD 3
#define SERIALNUM_4_CORRECT_CARD 75

extern speaker Speaker;
extern UART_HandleTypeDef huart1;
extern char Data;

void RFID_Init(rfid* sensor) {
    MFRC522_Init();
    memset(sensor->prevSerialNum, 0, 5);
    sensor->status = CARD_IDLE;

    sensor->botEnabled = false;
    sensor->initialSuccessfulCardTap = true;
    sensor->initialFailedCardTap = true;

    HAL_GPIO_WritePin(RFID_STATUS_GPIO_Port, RFID_STATUS_Pin, GPIO_PIN_SET);
}

rfid_card_status RFID_ValidateCard(rfid* sensor)
{
	uint8_t serialNum[5];
	MFRC522_Request(PICC_REQIDL, serialNum);
	MFRC522_Anticoll(serialNum);

	sensor->status = CARD_IDLE;

	if ((serialNum[0] == 170 && serialNum[1] == 205 && serialNum[2] == 47 && serialNum[3] == 3 && serialNum[4] == 75) ||
			(sensor->prevSerialNum[0] == 170 && sensor->prevSerialNum[1] == 205 && sensor->prevSerialNum[2] == 47 && sensor->prevSerialNum[3] == 3 && sensor->prevSerialNum[4] == 75))
	{
		sensor->status = CARD_SUCCESS;

	}
	else if (!(serialNum[0] | (!(serialNum[1] == 32 || serialNum[1] == 0)) | serialNum[2] | serialNum[3] | serialNum[4]))
	{
		if (!(sensor->prevSerialNum[0] | sensor->prevSerialNum[1] | sensor->prevSerialNum[2] | sensor->prevSerialNum[3] | sensor->prevSerialNum[4]))
			sensor->status = CARD_IDLE;
		else
		{
			sensor->status = CARD_FAIL;
		}

	}
	else
	{
		sensor->status = CARD_FAIL;
	}

	for (uint8_t i = 0; i < 5; i++)
	{
		sensor->prevSerialNum[i] = serialNum[i];
	}

	return sensor->status;
}

void RFID_SecurityLogic(rfid* sensor)
{
	rfid_card_status cardStatus = RFID_ValidateCard(sensor);

	switch (cardStatus) {
	    case CARD_SUCCESS:
	    	if (sensor->initialSuccessfulCardTap)
	    	{

	    		Speaker_SetAutoReload(&Speaker, 488);
	    		Speaker_Beep(&Speaker, 150, 0, 1);
	    		sensor->initialSuccessfulCardTap = false;
	    		sensor->initialFailedCardTap = true;
	    		sensor->botEnabled = !sensor->botEnabled;
	    		HAL_GPIO_WritePin(RFID_STATUS_GPIO_Port, RFID_STATUS_Pin, (GPIO_PinState) !sensor->botEnabled);
	    	}
	        break;

	    case CARD_FAIL:
	    	if (sensor->initialFailedCardTap)
	    	{
	    		HAL_Delay(200);
				if (RFID_ValidateCard(sensor) != CARD_FAIL)
					break;
				Speaker_SetAutoReload(&Speaker, 488 * 4);
				Speaker_Beep(&Speaker, 150, 50, 4);
				sensor->initialSuccessfulCardTap = true;
				sensor->initialFailedCardTap = false;

	    	}
	        break;

	    case CARD_IDLE:
	    	sensor->initialSuccessfulCardTap = true;
	    	sensor->initialFailedCardTap = true;
	        break;

	    // Optional: Default case if no case matches
	    default:
	        // Code to execute if none of the above cases match
	        break;
	}

}

\end{lstlisting}

\begin{lstlisting}[caption={Source Code : STM32 Speaker Firmware}, label={lst:stm32_speaker_code}]
#include "speaker.h"

#define CLK_SPEED 32000000
#define DEFAULT_AUTORELOAD 488

void Speaker_Init(speaker* speaker, rfid* rfid_struct, TIM_HandleTypeDef* timer)
{
	speaker->rfid_sensor = rfid_struct;
	speaker->timer = timer;

	speaker->hasFault = false;
	speaker->beepLengthOn = 0;
	speaker->beepLengthPeriod = 0;
	speaker->wantedNumBeeps = 0;
	speaker->currentNumBeeps = 0;
	speaker->timerCounter = 0;

	for (uint8_t i = 0; i < sizeof(speaker->featureFault) / sizeof(speaker->featureFault[0]); i++)
	{
		speaker->featureFault[i] = false;
	}

}

void Speaker_Start(speaker* speaker, uint8_t ID)
{

	speaker->featureFault[ID] = true;
	if ((speaker->featureFault[0] || speaker->featureFault[1] || speaker->featureFault[2]) && speaker->rfid_sensor->botEnabled)
	{
		speaker->hasFault = true;
		Speaker_SetAutoReload(speaker, DEFAULT_AUTORELOAD);
		HAL_TIM_PWM_Start(speaker->timer, TIM_CHANNEL_1);
	}

}

void Speaker_Stop(speaker* speaker, uint8_t ID)
{
	speaker->featureFault[ID] = false;
	if (!(speaker->featureFault[0] || speaker->featureFault[1] || speaker->featureFault[2]))
	{
		speaker->hasFault = false;
		HAL_TIM_PWM_Stop(speaker->timer, TIM_CHANNEL_1);
	}
}

bool Speaker_Beep(speaker* speaker, uint16_t length_on_ms, uint16_t length_off_ms, uint8_t numBeeps)
{

	if (speaker->hasFault)
		return false;

	speaker->timerCounter = 0;
	speaker->currentNumBeeps = 0;

	speaker->beepLengthOn = length_on_ms * 1000 / __HAL_TIM_GET_AUTORELOAD(speaker->timer);
	speaker->beepLengthPeriod =speaker->beepLengthOn + length_off_ms * 1000 / __HAL_TIM_GET_AUTORELOAD(speaker->timer);
	speaker->wantedNumBeeps = numBeeps;

	//speaker->beepLength = length_ms * CLK_SPEED / (speaker->timer->Instance->PSC);

	HAL_TIM_Base_Start_IT(speaker->timer);
	HAL_TIM_PWM_Start(speaker->timer, TIM_CHANNEL_1);
	return true;
}

void Speaker_BeepInterrupt(speaker* speaker)
{
    if (speaker->currentNumBeeps < speaker->wantedNumBeeps)
    {

        if (speaker->timerCounter == speaker->beepLengthOn)
        {
            HAL_TIM_PWM_Stop(speaker->timer, TIM_CHANNEL_1);
            __HAL_TIM_ENABLE(speaker->timer);
        }
        else if (speaker->timerCounter >= speaker->beepLengthPeriod)
        {
        	speaker->currentNumBeeps++;
			speaker->timerCounter = 0;

            if (speaker->currentNumBeeps < speaker->wantedNumBeeps)
            {
                HAL_TIM_PWM_Start(speaker->timer, TIM_CHANNEL_1);

            }

        }
        speaker->timerCounter++;
    }
    else
    {
        HAL_TIM_PWM_Stop(speaker->timer, TIM_CHANNEL_1);
        HAL_TIM_Base_Stop_IT(speaker->timer);
    }
}

void Speaker_SetAutoReload(speaker* speaker, uint16_t value)
{
	__HAL_TIM_SET_AUTORELOAD(speaker->timer, value);
	__HAL_TIM_SET_COMPARE(speaker->timer, TIM_CHANNEL_1, value / 2);
}

\end{lstlisting}

\begin{lstlisting}[caption={Source Code : Robot Driver App}, label={lst:driver_app_code}]
    import asyncio
    import threading

    from bleak import BleakScanner, BleakClient, BleakError
    from flask import Flask, request, jsonify, render_template

    class BLEManager:
        # Define UUIDs for BLE Service and Characteristic
        SERVICE_UUID = "00000000-5EC4-4083-81CD-A10B8D5CF6EC"
        CHARACTERISTIC_UUID = "00000001-5EC4-4083-81CD-A10B8D5CF6EC"
        CODE = "0095" # Authentication Code

        def __init__(self):
            self.devices = []
            self.client = None
            self.is_connected = False

            self.loop = asyncio.new_event_loop()
            self.start_loop()

        def start_loop(self):
            threading.Thread(target = self._run_loop, daemon = True).start()

        def _run_loop(self):
            asyncio.set_event_loop(self.loop)
            self.loop.run_forever()

        def run_async(self, coro):
            return asyncio.run_coroutine_threadsafe(coro, self.loop)

        async def scan_devices(self):
            self.devices = []
            scanned = await BleakScanner.discover()

            self.devices = [
                {"name" : device.name, "address" : device.address} for device in scanned if device.name and ("WALL-E" in device.name)
            ] # Filter BLE Devices
            return self.devices

        async def connect_device(self, address):
            """Connect to BLE Device."""
            if self.client and self.client.is_connected:
                self.is_connected = True
                return True

            self.client = BleakClient(address)
            try:
                await self.client.connect()
                await self.client.write_gatt_char(BLEManager.CHARACTERISTIC_UUID, BLEManager.CODE.encode("utf-8"))
                self.is_connected = self.client.is_connected
                return self.is_connected
            except BleakError:
                self.is_connected = False
                return False

        async def disconnect_device(self):
            """Disconnect from BLE Device."""
            if self.client and self.client.is_connected:
                await self.client.disconnect()
            self.is_connected = False

        async def send_cmd(self, cmd):
            """Schedule Send Command Coroutine Using Button's Custom Command."""
            if not (self.client and self.client.is_connected):
                return False, "Not Connected to BLE"
            try:
                await self.client.write_gatt_char(BLEManager.CHARACTERISTIC_UUID, cmd.encode("utf-8"))
                return True, f"Sent Command: {cmd}"
            except BleakError as e:
                return False, f"Error Sending Command: {e}"

    class RobotDriverApp:
        def __init__(self):
            self.app = Flask("Robot Driver App")
            self.ble_manager = BLEManager()
            self._register_routes()

        def _register_routes(self):
            @self.app.route("/")
            def index():
                return render_template("index.html")

            @self.app.route("/scan", methods = ["GET"])
            def scan():
                future = self.ble_manager.run_async(self.ble_manager.scan_devices())
                devices = future.result(timeout = 30) # Wait for 30 Seconds
                return jsonify(devices)

            @self.app.route("/connect", methods = ["POST"])
            def connect():
                data = request.get_json()
                if not data or "deviceAddress" not in data:
                    return jsonify({"error": "No Address Provided"}), 400
                future = self.ble_manager.run_async(self.ble_manager.connect_device(data["deviceAddress"]))
                success = future.result(timeout = 15) # Wait for 15 Seconds
                return (jsonify({"status": "Connected"}) if success
                        else (jsonify({"status": "Failed"}), 400))

            @self.app.route("/disconnect", methods = ["GET"])
            def disconnect():
                future = self.ble_manager.run_async(self.ble_manager.disconnect_device())
                future.result(timeout = 10) # Wait for 5 Seconds
                return jsonify({"status": "Disconnected"})

            @self.app.route("/move", methods = ["POST"])
            def move():
                data = request.get_json()
                if not data or "command" not in data:
                    return jsonify({"error": "No Command Provided"}), 400 # Bad Request

                future = self.ble_manager.run_async(
                    self.ble_manager.send_cmd(data["command"])
                )
                success, message = future.result(timeout = 10) # Wait for 5 Seconds

                if success:
                    return jsonify({"status": "OK", "msg": message})
                else:
                    return jsonify({"status": "Error", "msg": message}), 400 # Bad Request

        def run(self):
            self.app.run(host = "0.0.0.0", port = 5000, debug = False)

    if __name__ == "__main__":
        RobotDriverApp().run()
\end{lstlisting}

\begin{lstlisting}[caption={Source Code : PiCamera Display}, label={lst:picamera_display_code}]
from picamera2 import Picamera2
from picamera2.encoders import H264Encoder
from libcamera import Transform

class CameraDisplay(tk.Frame):
    SAMPLE_RATE = 1.0 / 50.0 # Update Delay ~20 FPS (1000ms/20 = 50ms)
    def __init__(self, parent, *args, **kwargs):
        super().__init__(parent, *args, **kwargs)

        self.filename = ""
        self.camera = Picamera2() # Init Camera

        self.snapshot_dir: str = os.path.join(os.path.dirname(os.path.abspath(__file__)), "Snapshots")
        self.video_dir: str = os.path.join(os.path.dirname(os.path.abspath(__file__)), "Videos")

        os.makedirs(self.snapshot_dir, exist_ok = True)
        os.makedirs(self.video_dir, exist_ok = True)

        # Force RGB888 Output
        self.config = self.camera.create_video_configuration(
            main = {
                "size": (640, 480), # Default Size
                # "size": (1280, 720), # HD
                # "size": (1920, 1080), # Full HD
                "format": "RGB888"
            },
            transform = Transform(hflip = False, vflip = False) # For Tkinter Display
        )
        self.image_label = tk.Label(self)
        self.image_label.pack()

    def start_recording(self):
        self.camera.configure(self.config)
        self.camera.start()

        self.filename = f"Recording_{dt.datetime.now().strftime('%Y%m%d_%H%M%S')}"
        input_file = os.path.join(self.video_dir, f"{self.filename}.h264")

        self.camera.start_recording(H264Encoder(bitrate = 10000000), input_file)

    def stop_recording(self):
        if self.filename == "":
            return

        self.camera.stop_recording()
        self.camera.stop()
        self.filename = ""

    def take_snapshot(self):
        if self.filename == "":
            self.camera.configure(self.config)
            self.camera.start()

        # Capture Current Frame
        frame = self.camera.capture_array()
        if frame is None or frame.size == 0:
            print("Failed to Capture Snapshot.")
            return

        # Swap Color Channels (BGR -> RGB)
        frame = frame[..., ::-1]

        snapshot_name = f"Snapshot_{dt.datetime.now().strftime('%Y%m%d_%H%M%S')}.jpg"
        snapshot_path = os.path.join(self.snapshot_dir, snapshot_name)

        # Convert to PIL Image
        image = PILImage.fromarray(frame)
        image.save(snapshot_path) # Save Image
        print(f"Snapshot Saved to {snapshot_path}")

        if self.filename == "":
            self.camera.stop()

    def update(self):
        if self.filename == "":
            return

        frame = self.camera.capture_array()
        if (frame is not None) and (frame.size != 0):
            frame = frame[..., ::-1] # BGR -> RGB

            # Convert the PIL Image to an ImageTk.PhotoImage
            self.image_label.current = ImageTk.PhotoImage(
                image = PILImage.fromarray(frame) # Convert Numpy Array to PIL.Image
            )
            self.image_label.configure(image = self.image_label.current)

    def stop(self):
        self.camera.close()
\end{lstlisting}

\begin{lstlisting}[caption={Source Code : Python Stripchart}, label={lst:stripchart_code}]
    class StripChart:
    # SAMPLE_RATE = 0.250 # 250 ms
    SAMPLE_RATE = 1 # 1000 ms
    def __init__(self, master, conn = None, data_size = 25, ylim = 30):
        self.master = master
        self.conn = conn
        self.fig, self.ax = plt.subplots(figsize = (900 / 100, 755 / 100))

        self.data_size, self.ylim = data_size, ylim

        # Angle Data (Additional Storage Preferred Over DataFrame for Speed)
        self.sample_data = []
        self.accelerometer_data = []
        self.gyroscope_data = []
        self.complementary_data = []

        # DataFrame for Data Export
        self.start_time = None
        self.data_df = pd.DataFrame(
            columns = [
                'Time (PST)',
                'Accelerometer Angle (Deg)',
                'Gyroscope Angle (Deg)',
                'Complementary Angle (Deg)'
            ]
        )

        self.ax.set_title('Real-Time Angle Strip-Chart')
        self.ax.grid(True)

        self.ax.set_xlim(
            0, # Start at 0s
            # 1.25 * self.data_size * StripChart.SAMPLE_RATE * 0.1
            1.25 * self.data_size * StripChart.SAMPLE_RATE
        )
        self.ax.set_xticks(
            np.arange(
                0,  # Start at 0s
                # 1.25 * self.data_size * StripChart.SAMPLE_RATE * 0.1,
                1.25 * self.data_size * StripChart.SAMPLE_RATE,
                5  # Set Ticks to 5s Intervals
            )
        )

        self.ax.set_ylim(-self.ylim, self.ylim) # Angle Expected to be Between -180 Deg and 180 Deg
        self.ax.set_yticks(np.arange(-self.ylim, self.ylim + 1, 5))

        self.ax.tick_params(axis = 'both', labelsize = 8)

        self.ax.set_xlabel('Time (s)')
        self.ax.set_ylabel('Angle (Deg)')

        self.accelerometer_line, = self.ax.plot([], [], linestyle = 'dashed', lw = 1.5, label = 'Accelerometer Angle (Deg)', color = 'lightblue')
        self.gyroscope_line, = self.ax.plot([], [], linestyle = 'dashed', lw = 1.5, label = 'Gyroscope Angle (Deg)', color = 'tomato')
        self.complementary_line, = self.ax.plot([], [], lw = 1.5, label = 'Complementary Angle (Deg)', color = 'purple')

        self.fig.subplots_adjust(bottom = 0.2)
        self.ax.legend(
            loc = 'upper center',
            bbox_to_anchor = (0.5, -0.15), # Position Above Plot with Padding
            ncol = 3, framealpha = 0.9,  # 3 Columns, Transparent Background
            fontsize = 10,
        )

        self.canvas = FigureCanvasTkAgg(self.fig, master=self.master)
        self.canvas_widget = self.canvas.get_tk_widget()

        self.figures_dir: str = os.path.join(os.path.dirname(os.path.abspath(__file__)), "Figures")
        self.logbook_dir: str = os.path.join(os.path.dirname(os.path.abspath(__file__)), "Logbook")

        os.makedirs(self.figures_dir, exist_ok = True)
        os.makedirs(self.logbook_dir, exist_ok = True)

    def start(self, conn):
        """Start StripChart."""
        self.conn = conn
        self.animation = animation.FuncAnimation(
            fig = self.fig, # Figure
            func = self.update, # Update Function
            frames = self.data_size, # Number of Frames
            blit = False, # Prevent Re-rendering Entire Plot
            interval = StripChart.SAMPLE_RATE * 1000, # Delay in ms
        )
        self.canvas = FigureCanvasTkAgg(self.fig, master = self.master)
        self.canvas_widget = self.canvas.get_tk_widget()

    def update(self, frame):
        """Update StripChart with New Data."""
        self.rx_angle()

        # Update Plot Data
        # t_data = [t * 0.1 for t in self.sample_data]
        t_data = [t for t in self.sample_data]
        self.accelerometer_line.set_data(t_data, self.accelerometer_data)
        self.gyroscope_line.set_data(t_data, self.gyroscope_data)
        self.complementary_line.set_data(t_data, self.complementary_data)

        # Adjust x Limits to Scroll Forward
        if (len(self.sample_data) > 0) and (self.sample_data[-1] > self.data_size):
            self.ax.set_xlim(
                t_data[0], # Start at First Data Point
                # t_data[0] + 1.25 * self.data_size * StripChart.SAMPLE_RATE * 0.1
                t_data[0] + 1.25 * self.data_size * StripChart.SAMPLE_RATE
            ) # Display 25% More Data
            self.ax.set_xticks(
                np.arange(
                    t_data[0], # Start at First Data Point
                    # t_data[0] + 1.25 * self.data_size * StripChart.SAMPLE_RATE * 0.1,
                    t_data[0] + 1.25 * self.data_size * StripChart.SAMPLE_RATE,
                    5  # Set Ticks to 5s Intervals
                )
            )
        else:
            self.ax.set_xlim(
                0, # Start at 0s
                # 1.25 * self.data_size * StripChart.SAMPLE_RATE * 0.1
                1.25 * self.data_size * StripChart.SAMPLE_RATE
            )
            self.ax.set_xticks(
                np.arange(
                    0,  # Start at 0s
                    # 1.25 * self.data_size * StripChart.SAMPLE_RATE * 0.1,
                    1.25 * self.data_size * StripChart.SAMPLE_RATE,
                    5  # Set Ticks to 5s Intervals
                )
            )

    def stop(self):
        """Set Connection to None and Stop Updating."""
        if self.conn is not None:
            self.conn.close()
            self.conn = None

            fig_name = f"Angle_Data_{dt.datetime.now().strftime('%Y%m%d_%H%M%S')}"
            self.save_logs(fig_name)
            self.save_fig(fig_name)

    def rx_angle(self):
        """Read Angle Data from Serial Connection."""
        def read_serial() :
            """Read Data from Serial Connection."""
            if (self.conn is not None) :
                return str(self.conn.readline().decode('ascii').strip('\r').strip('\n'))
            else :
                return None

        if self.conn is None:
            return

        try:
            self.conn.write(b'A')
        except serial.SerialException:
            self.conn.reconnect()

        try:
            arduinoStream: list = str(read_serial()).rstrip('\r').split(' ')
            if len(arduinoStream) != 3:
                 raise ValueError

            accelerometer_angle = float(arduinoStream[0])
            gyroscope_angle = float(arduinoStream[1])
            complementary_angle = float(arduinoStream[2])

            print(f"Accelerometer Angle: {accelerometer_angle} Deg")
            print(f"Gyroscope Angle: {gyroscope_angle} Deg")
            print(f"Complementary Angle: {complementary_angle} Deg")

            # Append Data
            new_sample = (self.sample_data[-1] + 1) if self.sample_data else 0

            self.sample_data.append(new_sample)
            self.accelerometer_data.append(accelerometer_angle)
            self.gyroscope_data.append(gyroscope_angle)
            self.complementary_data.append(complementary_angle)

            self.start_time = dt.datetime.now(pytz.timezone('US/Pacific')) if self.start_time is None else self.start_time

            if self.data_df.empty:
                self.data_df = pd.DataFrame({
                    'Time (PST)': self.start_time,
                    'Accelerometer Angle (Deg)': accelerometer_angle,
                    'Gyroscope Angle (Deg)': gyroscope_angle,
                    'Complementary Angle (Deg)': complementary_angle
                }, index = [0])
            else:
                self.data_df = pd.concat([
                    self.data_df,
                    pd.DataFrame([{
                        'Time (PST)': self.start_time + dt.timedelta(seconds = new_sample),
                        'Accelerometer Angle (Deg)': accelerometer_angle,
                        'Gyroscope Angle (Deg)': gyroscope_angle,
                        'Complementary Angle (Deg)': complementary_angle
                    }])], ignore_index = True
                )

        except serial.SerialException:
            self.conn.reconnect()
        except ValueError as value_error: # Parse Error
            display("Parse Error:", str(value_error))

        # Limit Size to Trailing Data
        self.sample_data = self.sample_data[-self.data_size:]
        self.accelerometer_data = self.accelerometer_data[-self.data_size:]
        self.gyroscope_data = self.gyroscope_data[-self.data_size:]
        self.complementary_data = self.complementary_data[-self.data_size:]

    def save_fig(self, fig_name) :
        """Save Figure to File."""
        file_path = os.path.join(self.figures_dir, f"{fig_name}.jpg")

        self.fig.savefig(file_path, format = 'jpg', dpi = 800)
        print(f"Figure Saved to {file_path}")

    def save_logs(self, file_name):
        """Save Data to CSV File."""
        file_path = os.path.join(self.logbook_dir, f"{file_name}.csv")

        csv_df = self.data_df.copy()
        csv_df['Time (PST)'] = self.data_df['Time (PST)'].dt.strftime('%Y-%m-%d %H:%M:%S')
        csv_df.to_csv(file_path, index = False)

        print(f"Data Exported to {file_path}\n\nData Preview:\n")
        display(self.data_df.head(2))
        display("--------------------")
        display(self.data_df.tail(2))
\end{lstlisting}

\end{document}

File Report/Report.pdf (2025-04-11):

# Self-Balancing Robot

Course: ELEC 391 201 2024W2

Authors: Team B-17 (Tomaz Zlindra, Muntakim Rahman, Xianyao Li)

Instructors: Dr. Joseph Yan and Dr. Cristian Grecu

Submission Date: April 13th, 2025

## Contents

1 Introduction | 3
2 Requirements, Specifications and Constraints | 3
3 Conceptual Design | 3
4 Subsystem Design | 5
5 Verification and Validation | 22
6 Conclusions and Future Work | 22
7 References | 22
8 Appendices | 22

## 1 Introduction

Description of the engineering problem or challenge Background context and any relevant history

## 2 Requirements, Specifications and Constraints

It’s helpful to list these in a table or enumerated, (e.g. R1, R2, etc.) so this can be treated as of checklist of requirements that must be tested as detailed in the Verification and Validation section.

### 2.1 Functional Requirements

The table below (1) lists all the functional requirements of the robot

ID | Requirement Description | Priority
FR1 | The robot must balance on a flat surface by controlling the DC motors. | Core
FR2 | The robot must maintain balance while driven externally on a flat surface. | Core
FR3 | The robot must maintain balance while turning at a reasonable speed. | Core
FR4 | The robot must move forward and backward under external control. | Core
FR5 | The robot must be controlled via Bluetooth with four directional commands. | Core
FR6 | The robot must maintain balance on a track with up to 15 degrees of incline. | Core
FR7 | The distance sensor must detect obstacles within 5-50 cm and stop the robot within 20 cm. | Additional Feature
FR8 | The color sensor must be able to detect at least red, green and blue colors | Additional Feature
FR9 | The RFID module must authenticate an RFID tag within 1 second to prevent unauthorized operation. | Additional Feature
FR10 | The Raspberry Pi Zero must process and transmit a camera feed at least 1 FPS. | Additional Feature

Table 1: Functional Requirements of the Self-Balancing Robot

### 2.2 Performance Requirements

Metrics for performance such as speed, efficiency, capacity, etc.

### 2.3 Constraints

(financial, temporal, material, environmental, standards and regulations to follow, etc.)

## 3 Conceptual Design

High level functional diagram/architecture of the overall system.

### 3.1 High-level Functional Diagram


Figure 1: High-level Functional Diagram

The functional diagram in Figure (1) highlights our system-design for enforcing secure access of the robot with RFID and Bluetooth Low Energy (BLE). We prevent users from balancing or moving the robot without the required authentication. Once successful, the firmware was programmed to prioritize safe operation of the robot, while accounting for environmental factors such as distance and color detection.

### 3.2 Architecture Diagram


Figure 2: Architecture Diagram

This might need to be updated. We should also add some text to explain what is going on

## 4 Subsystem Design

Detailed description and schematics for key subsystems
Include electrical, mechanical, structural, or process-related subsystems as appropriate

### 4.1 Structural Design
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

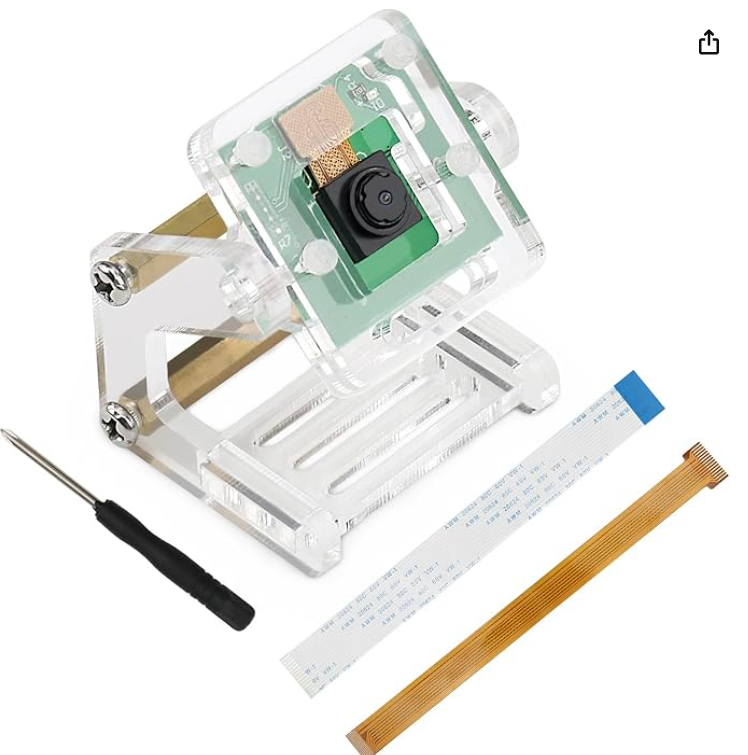
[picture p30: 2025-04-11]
Report/Figures/Freenove_Camera.png

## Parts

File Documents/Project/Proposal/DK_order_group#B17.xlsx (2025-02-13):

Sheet: Sheet1
Group#: B17 |  | Order only from Digikey Canada
Digikey part number | Qty | Availability | Extended Price | Description |  | Price
1188-SNS-HCSR04-ND | 2 | 8 | 2.81 | Distance Sensor (SENSOR OPTICAL 20-100CM TTL) |  | 5.62
751-VEML3328CT-ND | 1 | 8304 | 3.04 | Color Sensor I2C (RGBCIR COLOR SENSOR I2C OPLGA4) |  | 3.04
2648-SC1176-ND | 1 | 2984 | 22.75 | Raspberry Pi Zero 2 (SBC 1.0GHZ 4 CORE 512MB RAM) |  | 22.75
4411-CN0090-ND | 1 | 281 | 8.49 | RFID Reader Module (RC522 RFID MODULE) |  | 8.49
497-3436-5-ND | 1 | 1363 | 2.55 | High Current Voltage Regulator 5V (IC REG LINEAR 5V 3A TO220) |  | 2.55
 |  |  |  |  | Digikey Price | 42.45
NA - Purchasing from Amazon (Part Number B0BZYPBS17) | 1 | In Stock | 21.95 | Freenove 8MP Camera for Raspberry Pi 5 4 B 3 B+ A+ Zero 2 W with Adjustable Holder and Ribbon Cable, 120° Viewing Angle, 1080P 720P Output |  | 21.95
 |  |  |  |  | Total Price | 64.4

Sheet: Sheet2
Part | Manufacturer PN | Digikey PN | Link | Datasheet | Description | Quantity | Cost/Unit | Total Cost
Distance Sensor | SNS-HCSR04 | 1188-SNS-HCSR04-ND | Link (https://www.digikey.ca/en/products/detail/olimex-ltd/SNS-HCSR04/21662590) | Datasheet (https://cdn.sparkfun.com/datasheets/Sensors/Proximity/HCSR04.pdf) | SENSOR OPTICAL 20-100CM TTL | 2 | 2.81 | 5.62
Color Sensor I2C | VEML3328 | 751-VEML3328CT-ND | Link (https://www.digikey.ca/en/products/detail/vishay-semiconductor-opto-division/VEML3328/10673129) | Datasheet (https://www.vishay.com/docs/84968/veml3328.pdf) | RGBCIR COLOR SENSOR I2C OPLGA4 | 1 | 3.04 | 3.04
Raspberry Pi Zero 2 | SC1176 | 2648-SC1176-ND | Link (https://www.digikey.ca/en/products/detail/raspberry-pi/SC1176/15298147) | Datasheet (https://datasheets.raspberrypi.com/rpizero2/raspberry-pi-zero-2-w-product-brief.pdf) | SBC 1.0GHZ 4 CORE 512MB RAM | 1 | 22.75 | 22.75
RFID Reader Module | CN0090 | 4411-CN0090-ND | Link (https://www.digikey.ca/en/products/detail/sunfounder/CN0090/18668629) | Datasheet (https://mm.digikey.com/Volume0/opasdata/d220001/medias/docus/60/CN0090%20DATASHEET.pdf) | RC522 RFID MODULE | 1 | 8.49 | 8.49
High Current Voltage Regulator 5V | LD1085V50 | 497-3436-5-ND | Link (https://www.digikey.ca/en/products/detail/stmicroelectronics/LD1085V50/669220) | Datasheet (https://www.st.com/content/ccc/resource/technical/document/datasheet/d3/84/d5/f6/3c/23/40/7b/CD00001883.pdf/files/CD00001883.pdf/jcr:content/translations/en.C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) | IC REG LINEAR 5V 3A TO220 | 1 | 2.55 | 2.55
Raspberry Pi Camera | N/A | N/A | Link (https://www.amazon.ca/dp/B08Q34FKFY?ref_=pe_123916410_1039242100_fed_asin_title&th=1) | None | Freenove 5MP Camera for Raspberry Pi 5 4 B 3 B+ A+ Zero 2 W with Adjustable Holder and Ribbon Cable, 62° Viewing Angle, 1080P 720P Output | 1 | 16.95 | 16.95

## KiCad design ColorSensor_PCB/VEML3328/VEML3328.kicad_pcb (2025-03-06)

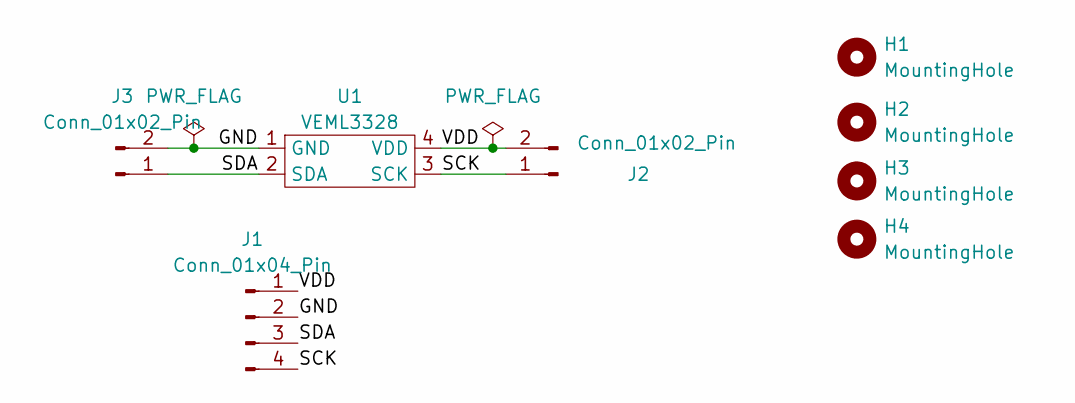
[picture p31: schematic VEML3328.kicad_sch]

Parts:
H1, H2, H3, H4: MountingHole; MountingHole_3.2mm_M3
J1: Conn_01x04_Pin; PinHeader_1x04_P2.54mm_Vertical
J2, J3: Conn_01x02_Pin; PinHeader_1x02_P2.54mm_Vertical
U1: VEML3328

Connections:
/GND: J1.2, J3.2 (Pin_1), U1.1 (GND)
/SCK: J1.4, J2.1, U1.3 (SCK)
/SDA: J1.3, J3.1 (Pin_2), U1.2 (SDA)
/VDD: J1.1, J2.2, U1.4 (VDD)

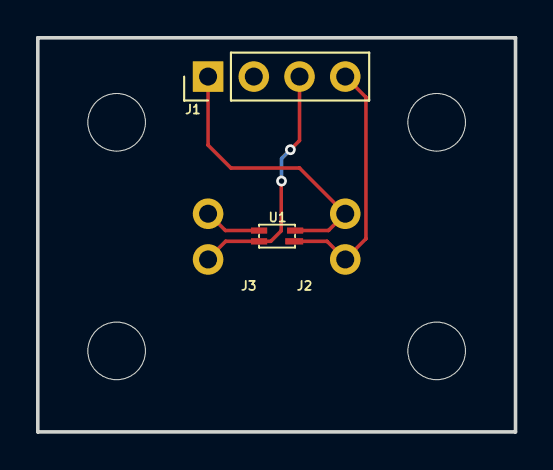
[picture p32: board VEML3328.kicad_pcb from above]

Board: 2 copper layers, 26.5 x 21.9 mm, 8 parts (0 on the bottom side), 4 nets.

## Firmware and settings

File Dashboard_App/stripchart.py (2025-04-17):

import os
import serial

import pandas as pd
import numpy as np
import math

import tkinter as tk

import matplotlib.pyplot as plt
from matplotlib.backends.backend_tkagg import FigureCanvasTkAgg
import matplotlib.animation as animation

import datetime as dt
import pytz

from IPython.display import display
class ArduinoSerial(serial.Serial) :
    PORT = '/dev/serial0'
    BAUDRATE = 115200
    def __init__(self, port = PORT, baudrate = 115200):
        super().__init__(port = port, baudrate = baudrate)

    def open(self) :
        super().open()
        if self.isOpen() :
            print('Serial Port is Open')
        else:
            print('Serial Port is Closed')

    def close(self) :
        super().close()
        print('Serial Port is Closed')

    def reconnect(self) :
        self.close()

        while not self.isOpen() :
            try:
                self.open()
            except:
                pass
        print('Serial Port is Open')

class StripChart:
    REQUEST_BYTE = b'A'
    def __init__(self, master, conn = None, data_size = 25, sample_rate = 0.1, ylim = 30):
        self.master = master
        self.conn = conn
        self.fig, self.ax = plt.subplots(figsize = (900 / 100, 755 / 100))

        self.data_size = data_size # Number of Samples to Display
        self.sample_rate = sample_rate
        self.ylim = ylim # Y-Axis Limits (Deg)

        self.refresh() # Refresh Data

        self.figures_dir: str = os.path.join(os.path.dirname(os.path.abspath(__file__)), "Figures")
        self.logbook_dir: str = os.path.join(os.path.dirname(os.path.abspath(__file__)), "Logbook")

        os.makedirs(self.figures_dir, exist_ok = True)
        os.makedirs(self.logbook_dir, exist_ok = True)

    def start(self, conn):
        """Start StripChart."""
        self.conn = conn
        self.animation = animation.FuncAnimation(
            fig = self.fig, # Figure
            func = self.update, # Update Function
            frames = self.data_size, # Number of Frames
            blit = False, # Prevent Re-rendering Entire Plot
            interval = self.sample_rate * 1000, # Delay in ms
        )
        self.canvas = FigureCanvasTkAgg(self.fig, master = self.master)
        self.canvas_widget = self.canvas.get_tk_widget()

    def update(self, frame):
        """Update StripChart with New Data."""
        self.rx_angle()

        # Update Plot Data
        self.accelerometer_line.set_data(self.sample_data, self.accelerometer_data)
        self.gyroscope_line.set_data(self.sample_data, self.gyroscope_data)
        self.complementary_line.set_data(self.sample_data, self.complementary_data)

        # Adjust x Limits to Scroll Forward
        if (len(self.sample_data) > 0) and (self.sample_data[-1] > self.data_size + 1):
            self.ax.set_xlim(
                self.sample_data[0], # Start at First Data Point
                self.sample_data[0] + 1.25 * self.data_size # Display 25% More Data
            )
        else:
            self.ax.set_xlim(1, 1.25 * self.data_size)

    def refresh(self):
        """Refresh Data from StripChart."""
        self.sample_data = []
        self.accelerometer_data = []
        self.gyroscope_data = []
        self.complementary_data = []

        self.data_df = pd.DataFrame(
            columns = [
                'Time (PST)',
                'Accelerometer Angle (Deg)',
                'Gyroscope Angle (Deg)',
                'Complementary Angle (Deg)'
            ]
        )

        self.ax.cla()

        self.ax.set_title('Real-Time Angle Strip-Chart')
        self.ax.grid(True)

        self.ax.set_xlim(1, 1.25 * self.data_size)
        self.ax.xaxis.set_major_locator(plt.MultipleLocator(5))

        self.ax.set_ylim(-self.ylim, self.ylim) # Angle Expected to be Between -180 Deg and 180 Deg
        self.ax.set_yticks(np.arange(-self.ylim, self.ylim + 1, 5))

        self.ax.tick_params(axis = 'both', labelsize = 8)

        self.ax.set_xlabel('Sample (#)')
        self.ax.set_ylabel('Angle (Deg)')

        self.accelerometer_line, = self.ax.plot([], [], linestyle = 'dashed', lw = 1.5, label = 'Accelerometer Angle (Deg)', color = 'lightblue')
        self.gyroscope_line, = self.ax.plot([], [], linestyle = 'dashed', lw = 1.5, label = 'Gyroscope Angle (Deg)', color = 'tomato')
        self.complementary_line, = self.ax.plot([], [], lw = 1.5, label = 'Complementary Angle (Deg)', color = 'purple')

        self.fig.subplots_adjust(bottom = 0.2)
        self.ax.legend(
            loc = 'upper center',
            bbox_to_anchor = (0.5, -0.15), # Position Above Plot with Padding
            ncol = 3, framealpha = 0.9,  # 3 Columns, Transparent Background
            fontsize = 10,
        )

        self.canvas = FigureCanvasTkAgg(self.fig, master=self.master)
        self.canvas_widget = self.canvas.get_tk_widget()

    def stop(self):
        """Set Connection to None and Stop Updating."""
        if self.conn is not None:
            self.conn.close()
            self.conn = None

        if hasattr(self, 'animation') and self.animation:
            self.animation.event_source.stop()
            self.animation = None

    def save(self):
        fig_name = f"Angle_Data_{dt.datetime.now().strftime('%Y%m%d_%H%M%S')}"
        self.save_logs(fig_name)
        self.save_fig(fig_name)

    def rx_angle(self):
        """Read Angle Data from Serial Connection."""
        def decode(incoming) :
            """Read Data from Serial Connection."""
            decoded = None
            if (self.conn is not None) and (incoming is not None):
                try:
                    decoded = str(incoming.decode('ascii')).strip('\r').strip('\n')
                except UnicodeDecodeError:
                    decoded = None
            return decoded

        if self.conn is None:
            return

        # Request Data from Arduino
        try:
            # print("TX Byte:", StripChart.REQUEST_BYTE)
            self.conn.write(StripChart.REQUEST_BYTE)
        except serial.SerialException:
            self.conn.reconnect()

        try:
            incoming = self.conn.readline()
            # print(f"Incoming Data: {incoming}")

            decoded = decode(incoming)
            # print(f"Decoded Data: {decoded}")

            if decoded is None:
                raise ValueError(f"Received Invalid: {incoming}")

            arduinoStream: list = str(decode(incoming)).split(' ')
            if len(arduinoStream) != 3:
                 raise ValueError

            accelerometer_angle = float(arduinoStream[0])
            gyroscope_angle = float(arduinoStream[1])
            complementary_angle = float(arduinoStream[2])

            print(f"Accelerometer Angle: {accelerometer_angle} (Deg)")
            print(f"Gyroscope Angle: {gyroscope_angle} (Deg)")
            print(f"Complementary Angle: {complementary_angle} (Deg)")

            # Append Data
            new_sample = (self.sample_data[-1] + 1) if self.sample_data else 1

            self.sample_data.append(new_sample)
            self.accelerometer_data.append(accelerometer_angle)
            self.gyroscope_data.append(gyroscope_angle)
            self.complementary_data.append(complementary_angle)

            if self.data_df.empty:
                self.data_df = pd.DataFrame({
                    'Time (PST)': dt.datetime.now(pytz.timezone('US/Pacific')),
                    'Accelerometer Angle (Deg)': accelerometer_angle,
                    'Gyroscope Angle (Deg)': gyroscope_angle,
                    'Complementary Angle (Deg)': complementary_angle
                }, index = [0])
            else:
                self.data_df = pd.concat([
                    self.data_df,
                    pd.DataFrame([{
                        'Time (PST)': dt.datetime.now(pytz.timezone('US/Pacific')),
                        'Accelerometer Angle (Deg)': accelerometer_angle,
                        'Gyroscope Angle (Deg)': gyroscope_angle,
                        'Complementary Angle (Deg)': complementary_angle
                    }])], ignore_index = True
                )
        except serial.SerialException:
            self.conn.reconnect()
        except ValueError as value_error: # Parse Error
            display("Parse Error:", str(value_error))

        # Limit Size to Trailing Data
        self.sample_data = self.sample_data[-self.data_size:]
        self.accelerometer_data = self.accelerometer_data[-self.data_size:]
        self.gyroscope_data = self.gyroscope_data[-self.data_size:]
        self.complementary_data = self.complementary_data[-self.data_size:]

    def save_fig(self, fig_name) :
        """Save Figure to File."""
        file_path = os.path.join(self.figures_dir, f"{fig_name}.jpg")

        self.fig.savefig(file_path, format = 'jpg', dpi = 800)
        print(f"Figure Saved to {file_path}")

    def save_logs(self, file_name):
        """Save Data to CSV File."""
        file_path = os.path.join(self.logbook_dir, f"{file_name}.csv")

        csv_df = self.data_df.copy()
        csv_df['Time (PST)'] = self.data_df['Time (PST)'].dt.strftime('%H:%M:%S.%f').str[:-3]
        csv_df.to_csv(file_path, index = False)

        print(f"Data Exported to {file_path}\n\nData Preview:\n")
        display(self.data_df.head(2))
        display("--------------------")
        display(self.data_df.tail(2))

class StripchartApp(tk.Tk):
    def __init__(self):
        super().__init__()
        self.title("Stripchart App")
        # self.geometry("1000x850")
        # self.resizable(False, False)

        self.dashboard_frame = tk.Frame(self, bg = '#000000')
        self.serial_frame = tk.Frame(self.dashboard_frame)
        self.stripchart_frame = tk.Frame(self.dashboard_frame)

        ############################
        ### Serial Frame Widgets ###
        ############################

        self.port_label = tk.Label(self.serial_frame, text = "Serial Line : ", bg = '#787882')
        self.port_entry = tk.Entry(self.serial_frame, bg = '#6e9eeb')
        self.port_entry.insert(0, ArduinoSerial.PORT)

        self.baudrate_label = tk.Label(self.serial_frame, text = "Speed : ", bg = '#787882')
        self.baudrate_entry = tk.Entry(self.serial_frame, bg = '#6e9eeb')
        self.baudrate_entry.insert(0, str(ArduinoSerial.BAUDRATE))

        self.port_entry.bind("<Return>", lambda event: self.open_serial())
        self.baudrate_entry.bind("<Return>", lambda event: self.open_serial())
        self.open_button = tk.Button(
            self.serial_frame, text = "Open", command = self.open_serial, bg = '#6e9eeb',
        )

        self.port_label.grid(
            row = 0, column = 0,
            columnspan = 2,
            padx = 10, pady = 10,
            sticky = tk.EW
        )
        self.port_entry.grid(
            row = 0, column = 2,
            columnspan = 1,
            padx = 10, pady = 10,
            sticky = tk.EW
        )

        self.baudrate_label.grid(
            row = 0, column = 3,
            columnspan = 2,
            padx = 10, pady = 10,
            sticky = tk.EW
        )
        self.baudrate_entry.grid(
            row = 0, column = 5,
            columnspan = 1,
            padx = 10, pady = 10,
            sticky = tk.EW
        )

        self.open_button.grid(
            row = 0, column = 6,
            columnspan = 2,
            padx = 10, pady = 10,
            sticky = tk.EW
        )

        self.serial_frame.grid_rowconfigure(0, weight = 1)

        self.serial_frame.grid_columnconfigure(0, weight = 1)
        self.serial_frame.grid_columnconfigure(1, weight = 1)
        self.serial_frame.grid_columnconfigure(2, weight = 0)

        self.serial_frame.grid_columnconfigure(3, weight = 1)
        self.serial_frame.grid_columnconfigure(4, weight = 1)
        self.serial_frame.grid_columnconfigure(5, weight = 0)

        self.serial_frame.grid_columnconfigure(6, weight = 2)

        ################################
        ### StripChart Frame Widgets ###
        ################################

        self.stripchart = StripChart(self.stripchart_frame)
        self.save_button = tk.Button(
            self.stripchart_frame, text = "Save", command = self.save_data, bg = '#6e9eeb',
        )

        self.stripchart.canvas_widget.grid(row = 0, column = 0)
        self.save_button.grid(
            row = 1, column = 0,
            padx = 10, pady = 10,
            sticky = tk.EW
        )

        # Position Widgets

        self.serial_frame.grid(row = 0, column = 0, padx = 10, pady = 10, sticky = tk.NSEW)
        self.stripchart_frame.grid(row = 1, column = 0, padx = 10, pady = 10, sticky = tk.NSEW)

        self.dashboard_frame.grid_rowconfigure(0, weight = 1)
        self.dashboard_frame.pack(fill = tk.BOTH, expand = True)

        self.protocol("WM_DELETE_WINDOW", self.on_close) # Cleanup

    def open_serial(self):
        port = self.port_entry.get()
        baudrate = self.baudrate_entry.get()

        try :
            self.conn = ArduinoSerial(
                port = port, baudrate = int(baudrate)
            )

            self.stripchart.start(self.conn) # Start StripChart
            self.stripchart.canvas_widget.grid(row = 0, column = 0)
            self.open_button.config(text = "Close", command = self.close_serial, bg = '#f06e47')
        except serial.SerialException as serial_error:
            print("Serial Connection Error:", str(serial_error))
            self.conn = None
            self.open_button.config(text = "Open", command = self.open_serial, bg = '#6e9eeb')

    def close_serial(self):
        if self.stripchart.conn is not None:
            self.stripchart.stop()
            self.stripchart.refresh() # Refresh Data
            self.open_button.config(text = "Open", command = self.open_serial, bg = '#6e9eeb')

    def save_data(self):
        if not self.stripchart.data_df.empty:
            self.stripchart.save()
        else:
            print("No Data Available")

    def on_close(self):
        """Close Serial Connection on Application Exit."""
        self.close_serial()
        self.save_data()

        # Exit Application
        self.destroy()

if __name__ == "__main__":
    StripchartApp().mainloop()

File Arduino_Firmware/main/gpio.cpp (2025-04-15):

#include "gpio.h"

bool stmConnected = false;
bool forwardAlert = false;
bool reverseAlert = false;
bool botEnabled = false;
bool redAlert = false;

void setupGPIO() {
    pinMode(PIN_STM32, INPUT_PULLUP);
    if (digitalRead(PIN_STM32) == HIGH) {
        Serial.println("STM32 Not Connected!");
        stmConnected = false; // STM32 Connected
        return; // STM32 Not Connected
    } else {
        Serial.println("STM32 Connected!");
        stmConnected = true; // STM32 Connected

        pinMode(PIN_RFID_DISABLED, INPUT_PULLUP);
        pinMode(PIN_RED_ALERT, INPUT_PULLUP);
        pinMode(PIN_FORWARD_ALERT, INPUT_PULLUP);
        pinMode(PIN_REVERSE_ALERT, INPUT_PULLUP);
    }
}

void checkRFID() {
    if (digitalRead(PIN_RFID_DISABLED) == LOW) botEnabled = true;
    else botEnabled = false;
}

void checkRedAlert() {
    if (digitalRead(PIN_RED_ALERT) == LOW) redAlert = true;
    else redAlert = false;
}

void checkForwardAlert() {
    if (digitalRead(PIN_FORWARD_ALERT) == LOW) forwardAlert = true;
    else forwardAlert = false;
}

void checkReverseAlert() {
    if (digitalRead(PIN_REVERSE_ALERT) == LOW) reverseAlert = true;
    else reverseAlert = false;
}

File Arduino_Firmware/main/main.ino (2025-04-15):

#include <Arduino.h>

#include "angle.h"
#include "controller.h"
#include "ble.h"
#include "serial.h"
#include "gpio.h"
#include "driver.h"

void setup() {
  setupSerial();
  setupGPIO();

  setupIMU();
  setupBLE();

  setupMotors();

  Serial.println("Setup Complete!");
}

void loop() {
  checkEventBLE(); // Check BLE Connection for New Events

  if (stmConnected) {
    checkRFID(); // Check RFID Status
    checkForwardAlert();
    checkReverseAlert();
    checkRedAlert();
  } else {
    botEnabled = true; // Default to Enabled if STM32 Not Connected
  }

  if (!botEnabled) {
    moveForward(0); // Stop Motors
    return; // Exit Function
  } else if (!isAuthenticated) {
    moveForward(0); // Stop Motors
    if (!isPromptedBLE) {
      customCharacteristic.writeValue("Enter Code:"); // Send BLE Prompt
      isPromptedBLE = true; // Set BLE Prompt Flag
    }
    return; // Exit Function
  }

  // Control Loop
  getAngles(Angles);
  balanceRobot(bleDirection);

  // updateParamSerial();

  // Send Data
  serialMsg = String(Angles.Accelerometer, 2) + " " +
    String(Angles.Gyroscope, 2) + " " +
    String(Angles.Complementary, 2);
  handleData('A', serialMsg);
}

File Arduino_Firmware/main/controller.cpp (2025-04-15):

#include "controller.h"

const int VCC = 10.4; // 10.4 V

/* PID Controller Variables */
float SETPOINT_0; // Setpoint for PID Controller
float setpointAngle; // Reference Value, r_t (Angle = 180°)
float measuredAngle; // Output Value, y_t (Angle)

float errorAngle; // Error Value, e_t = r_t - y_t
float prevErrorAngle; // Previous Error Value, e_(t-1)

float Kp; // Proportional Gain
float Ki; // Integral Gain
float Kd; // Derivative Gain

float errorAccumulation; // Accumulated Error Value, ∑e_t
float errorDifference; // Derivative Error Value, e_t - e_(t-1) / dt
float u_t; // Control Signal

float currDutyCycle; // Current PWM Duty Cycle
int bleDirection; // Current Direction

void setupController() {
    Kp = 0.7; // Proportional Gain
    Ki = 11.25; // Integral Gain
    Kd = 0.055; // Derivative Gain

    SETPOINT_0 = -0.15;
    setpointAngle = SETPOINT_0; // Reference Value, r_t (Angle = 180°)
    errorAngle = 0.0; // Error Value, e_t = r_t - y_t
    prevErrorAngle = 0.0; // Previous Error Value, e_(t-1)

    u_t = 0.0; // Control Signal
    errorAccumulation = 0.0; // Accumulated Error Value, ∑e_t
    errorDifference = 0.0; // Derivative Error Value, e_t - e_(t-1) / dt

    bleDirection = IDLE; // Set Default Direction
    currDutyCycle = 0.5; // Set Default PWM Value

    pinMode(DISABLE_INTEGRAL_BUTTON, INPUT_PULLUP);
}

void setupMotors() {
    setupPWM(); // Initialize PWM Pins
    setupController(); // Initialize PID Controller
    Serial.println("Motors Initialized!");
}

void balanceRobot(int bleDirection) {
    // Get Measured Angle
    measuredAngle = Angles.Complementary; // Complementary Filter
    errorAngle = setpointAngle - measuredAngle; // e_t = r_t - y_t
    errorDifference = (errorAngle - prevErrorAngle) / dt; // e_t - e_(t-1) / dt
    errorAccumulation += (errorAngle * dt);

    // Reset Accumulated Error Value ∑e_t
    if (digitalRead(DISABLE_INTEGRAL_BUTTON) == LOW) errorAccumulation = 0;

    // Calculate Control Signal : u_t = Kp * e_t + Ki * ∑e_t + Kd * (e_t - e_(t-1) / dt)
    u_t = (Kp * errorAngle) + (Ki * errorAccumulation) + (Kd * errorDifference);
    drive(u_t, errorAngle);

    prevErrorAngle = errorAngle; // Update Previous Error Value
    return;
}

void updateParamBLE(const char* bleBuff) {
    char paramType[STD_BUFFSIZE] = {0};
    char valueStr[STD_BUFFSIZE] = {0};
    float newValue = 0.0f;

    char returnStr[STD_BUFFSIZE] = {0};

    char cmd[STD_BUFFSIZE] = {0};
    strcpy(cmd, bleBuff); // Copy Command to Local Buffer

    int start = 0;
    while ((cmd[start] == ' ') || (cmd[start] == '\t')) start++; // Skip Leading Whitespace

    if (
      strncmp(&cmd[start], "k=", 2) == 0 ||
      strncmp(&cmd[start], "set=", 4) == 0 ||
      strncmp(&cmd[start], "Kp=", 3) == 0 ||
      strncmp(&cmd[start], "Ki=", 3) == 0 ||
      strncmp(&cmd[start], "Kd=", 3) == 0
    ) {
      char* equalsPos = strchr(&cmd[start], '='); // Find '=' Position
      if (!equalsPos) return;

      int paramLength = equalsPos - &cmd[start]; // Length of Parameter Name
      strncpy(paramType, &cmd[start], paramLength); // Copy Parameter Name
      paramType[paramLength] = '\0'; // Null-Termination

      strcpy(valueStr, equalsPos + 1); // Copy Value String
      newValue = atof(valueStr); // Convert Value String to Float

      if (strcmp(paramType, "k") == 0) k = newValue;
      else if (strcmp(paramType, "set") == 0) SETPOINT_0 = newValue;
      else if (strcmp(paramType, "Kp") == 0) Kp = newValue;
      else if (strcmp(paramType, "Ki") == 0) Ki = newValue;
      else if (strcmp(paramType, "Kd") == 0) Kd = newValue;
      else return; // Invalid Command

      sprintf(returnStr, "NewVal: %s=%s", paramType, valueStr);
      customCharacteristic.writeValue(returnStr);
    }
    return; // Exit Function
}


void updateParamSerial() {
    int parseIndex;
    String paramType, valueStr;
    if (Serial.available() > 0) {
      // Check for PID Parameter Update Command
      String command = Serial.readStringUntil('\n');
      command.trim(); // Remove Leading/Trailing Whitespace

      if (
        command.startsWith("k=") ||
        command.startsWith("set=") ||
        command.startsWith("Kp=") ||
        command.startsWith("Ki=") ||
        command.startsWith("Kd=")
      ) {
        parseIndex = command.indexOf('=');
        paramType = command.substring(0, parseIndex);
        valueStr = command.substring(parseIndex + 1);

        float newValue = valueStr.toFloat();

        if (valueStr != "0" && newValue == 0) {
          Serial.println("Invalid Value!");
          return;
        }

        if (paramType == "k") k = newValue;
        else if (paramType == "set") SETPOINT_0 = newValue;
        else if (paramType == "Kp") Kp = newValue;
        else if (paramType == "Ki") Ki = newValue;
        else if (paramType == "Kd") Kd = newValue;

        Serial.print("\r\nk: ");
        Serial.print(k, 3);
        Serial.print(" Setpoint: ");
        Serial.println(setpointAngle, 3);

        Serial.print("Kp: ");
        Serial.print(Kp, 4);
        Serial.print(" Ki: ");
        Serial.print(Ki, 4);
        Serial.print(" Kd: ");
        Serial.print(Kd, 4);
      }
    }
  }

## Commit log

2025-01-28 PWM is partially PWMing. Using mbed OS.
    Something weird with frequency.
2025-01-29 PWM is PWMing with 20 µs
2025-02-07 Functions for PWM
2025-02-10 All Directions Working, But One Wheel Slower RPM.
    ToDo: Test Decay, Test Angle Dependency, Integrate BLE
2025-02-10 Switched AIN, BIN by Board
2025-02-10 Cleaned up Code with Motor Pin Structs and General PWM UDF
2025-02-10 Fixed Angle Bug -> Had Unintentionally Commented Out Angle Assignments
    [main.ino]
2025-02-10 Angle Dependent PWM Adjustment
2025-02-10 Completed PWM, Angles (Excluding Accurate Movement Response, PWM to RPM Calibration)
2025-02-11 BLE Functioning, PWM Functioning, Angle Correct Calculation, Need to Develop App and Understand how to Measure Rotations with Hall Sensor. Also Build Floor 2
    [main.ino]
2025-02-11 Dashboard Page is Causing Blocking Issues with Latency for BLE
    [main.py]
2025-02-11 Need to Implement Firmware for Ensuring Data Transferred Once BLE Connection Established or Prevent Serial Until Established
    [main.py]
2025-02-12 End of Day 2025-02-11
    BLE and Serial Not Cooperating
    Got ~29%, 50%, 75%, 100% RPM (Minimum With Current is 29%)
    Robot Built
2025-02-12 Added Hall Sensor Measurement Rig STM Project
2025-02-13 End of Day 2025-02-12
    Functioning BLE - UART (Issue was with Firmware Forever Loop)
    Ready for Proof of Concept Demo
    [DK_order_group#B17.xlsx]
2025-02-13 Using venv for Raspberry Pi
    [DK_order_group#B17.xlsx]
2025-02-25 Added PWM BoilerPlate Code. Need to Test (i.e. Time Works, Angle Measured, Receiving BLE Commands, Etc. -> Integration Test)
2025-02-27 PID Does Not Appear to Have Broken Any Functionality
    [main.ino]
2025-02-27 Distance Sensor Works
2025-03-03 Updating with Changes from main, Raspberry_Pi
2025-03-04 Updating Driver App
2025-03-04 Speaker Code, fixed small issues with distance sensor code, all for G0
    [ExtraFeatures.ioc, ExtraFeatures_G0_Test.ioc, colorsensor.c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]
2025-03-05 Going to Rework and Replace Dashboard App
    [camera.py, main.py, stripchart.py]
2025-03-05 New Logic for Sample Time. Test and Update Angle Bounds
2025-03-06 Adding Dashboard App with Camera Features
2025-03-06 RFID complete, some new Speaker methods, still need to complete speaker firmware with RFID
    [VEML3328-B_Cu.gbr, VEML3328-B_Mask.gbr, VEML3328-B_Paste.gbr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]
2025-03-11 PID tuning 3/11/2025
2025-03-12 Working on STM32_Integration
2025-03-12 Testing for Toggle Pin
2025-03-12 GPIO to Arduino
2025-03-13 Testing Interrupt
2025-03-13 Trying to Integrate ISR. Working with Current Files. Add Rest of Firmware
2025-03-13 Seems to Be Working with PWM
2025-03-15 ISR Integrated, STM32 RFID Pin Added (Using for ISR Testing Right Now)
2025-03-16 Running at 20 Hz
2025-03-16 Applying and Testing PWM with ISR
2025-03-16 Updating for MATLAB Model. Running ISR at 50 Hz
2025-03-17 accidentally put stm32 code on raspberrypi_uart branch
2025-03-19 Color Sensor not working, but otherwise everything else should work
    [ExtraFeatures.ioc, colorsensor.c, main.c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]
2025-03-20 Ki 1.75 Seems Like Max Without Overshoot
    [main.ino]
2025-03-20 Ready for Driver Development
2025-03-21 Need to Improve IMU Sample Rate
2025-03-21 Updated to Include X Button
2025-03-24 Committing and Merging PID
2025-03-25 trying to tune PID
2025-03-25 a few minor PID changes
2025-03-27 PID Testing
2025-03-28 Bug with Kp, Ki, Kd Assignments
    [main.ino]
2025-04-01 did update on stm32cubeIDE
2025-04-03 Movement is Ok. Need to Integrate STM32
2025-04-03 Ready for STM32 Integration
2025-04-04 Movement and STM32 Integrated. Need to Tweak Balancing and Movement
2025-04-04 color sensor commented out
2025-04-06 Added new GPIO to Arduino with Colorsensor
2025-04-06 Added Pin Adjustment
2025-04-08 Added Raspberry Pi App + S3 Code
2025-04-15 Removing Unused Vars, Fixing Cmd App with Lock Screen, Working on Fixing Stripchart Delay
    [main.ino, stripchart.py]
2025-04-15 Updated Connection Button, Text Entry. Need to Add Password
2025-04-15 Added Logout Button
2025-04-16 Fixed ScanButton Bug in Driver App. Stripchart is Perfect on Desktop. Need to Fix for Raspberry Pi
    [stripchart.py]
2025-04-16 Testing on Raspberry Pi
2025-04-17 Testing Comms with Pi-Arduino
2025-04-17 Found General Issue:
    Raspberry Pi UART Works With Loopback.
    Arduino Cannot Receive the b'A' Being Sent from Raspberry Pi
    [ble.cpp, controller.cpp, gpio.cpp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]
2025-04-17 Retrieved all S3 Files
    [Angle_Data_20250416_225152.csv, Angle_Data_20250416_225225.csv]
